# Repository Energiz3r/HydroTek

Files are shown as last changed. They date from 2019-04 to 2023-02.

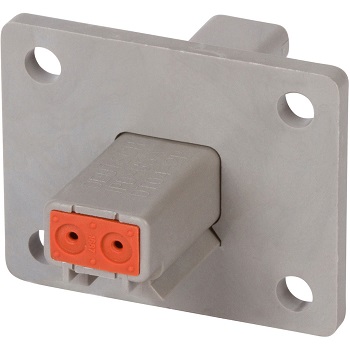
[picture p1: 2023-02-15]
pcb/DT04-2P-L012_1_1200__03789.jpg

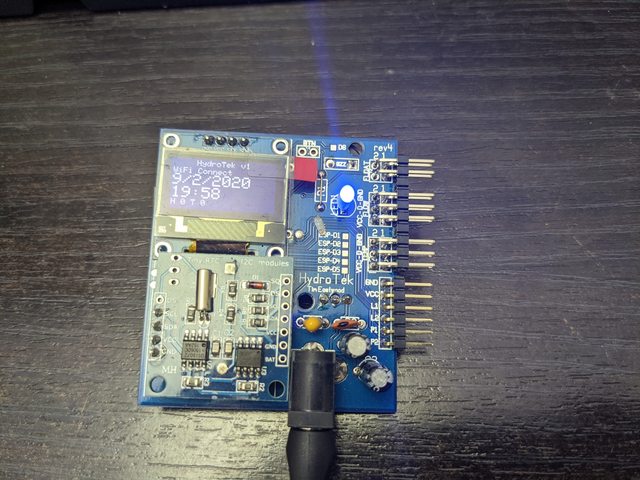
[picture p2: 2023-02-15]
pcb/rev4.jpg

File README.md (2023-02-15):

# HydroTek

## An IoT Controller for Aquaponics, Hydroponics, and Aeroponics

---

Visit [https://github.com/Energiz3r/hydrotek-react](https://github.com/Energiz3r/hydrotek-react) to access the react app which accompanies the hardware.

### Status Update:

This project is under development. If you wish to build this you should contact me to see if it's feasible at the time.
As of writing, the hardware is mostly complete, but I am designing a new PCB to address quality of life points, such as proper connectors for sensors instead of IDC header pins.
Firmware is largely finished and, with an understanding of the format of the web requests, could be made to talk to any API for updating the device configuration or just simply logging of data.
Management and reporting software comes in the form of a react / PHP / SQL based web app and is only partially complete.
Designs for the casing of the device will not be started until the PCB for the current revision is finalised and tested.

---

### Design:

There are four components to this repository:

- PCB cad file (created in PCBWeb for early revisions, then KiCad as of rev7)
- Firmware for the ESP32
- STL files for a case
- The webb app for configuration and monitoring of the device

### History:

Early revisions used an ESP8266 and an Arduino Nano, which communicated with each other over serial. Since discovering the ESP32 I've changed the design to simplify it greatly, however I suffered a consistent issue with the gerber files produced by PCBWeb which is now abandonware. New revisions are made in KiCAD.

---

### Overview:

This device is designed to control lighting and nutrient delivery in a hydroponics environment. It has been designed for use primarily with my own run-to-waste hydroponic system, however could be applied to just about any setup where the same sensors and control outputs are relevant, such as airponics, aquaponics, or even a simple vegge patch.

It's flexible enough that I've also used this to control the temperature within an enclosed container for making bread dough!

---

_latest hardware revision: 7_

(rev6 pictured below)
Powered here by USB - barrel jack connector not installed.



(rev5 pictured below)



(rev4 pictured below)



(rev3 pictured below)



---

## Device Options Menu (rev5):

https://www.youtube.com/watch?v=8toKR6Uxk_A

### Features:

- Uploads sensor data to cloud via WiFi
- 128x64 OLED display
- RTC with battery backup for control of grow light times even while offline or after power outage
- Online RTC time updates for accurate timekeeping
- Can monitor:
  - DHT22 temperature / humidity sensor
  - Liquid flow sensor (YF-S201 or any 5V based hall-effect sensor)
  - Float switch to detect either empty nutrient tank or full run-off tank
- Can control:
  - Grow light
  - Nutrient pump
- Buzzer / LED to alert user to lost WiFi signal, temperature extremes, nutrient pump faults, or full / empty nutrient / run-off tanks
- The board can be powered either through the barrel jack as designed or using a USB power source plugged into the ESP32 (Note: some USB power sources may not be sufficient to run both the HydroTek as well as relays connected)

I2C pH sensors _could_ be connected using a kit [such as this](https://www.sparkfun.com/products/10972), however pH meters are supposed to be stored in a pH-neutral storage solution. Since this means they aren't suitable for a constant-monitoring setup, pH monitoring was excluded from the feature set.

---

### Design considerations:

- The device must be maintenance-free
- Once assembled, flashed, and configured, the device must be easy to set up and use by non-technical people
- Compact size desirable. Other off-the-shelf units or open-source setups seem to be quite large

---

### To Do (not started):

- finish API development to complete the feature of updating the device configuration as changes are made to it through the web interface
- update the RTC time from online
- WiFi configuration on the device, using buttons and a menu instead of by editing the sketch
- Flow sensor calibration on the device, eg. 'pour 1L of water through the sensor then press OK'

---

### PCB Build instructions:

Note: The capacitors, barrel jack, and LM7805 can be omitted if the intention is to only run HydroTek from a reliable USB power source.

_(rev5)_

- To manufacture the PCB, upload the gerber files for the current PCB revision to a service such as [DirtyPCBs](http://dirtypcbs.com/store/pcbs)
- Purchase the components, as desired, outlined in the BOM file
- Solder the components to the PCB, ensuring the following order is observed (_B/S = BOTTOM SIDE_):
  - (B/S) Solder the LM7805 linear regulator to the UNDERSIDE of the board, ensuring the tab is soldered to the large square pad for heat dissipation
  - Solder in the 4x capacitors
  - Solder in the piezo buzzer
  - Solder in the IDC headers for the sensor inputs (to the TOP side of the board)
  - Solder in the IDC sockets for the LCD (or alternatively, solder the LCD direct to the board, if clearance above capacitors allows)
  - Solder in the ESP32
  - Solder remaining components
  - Install IDC jumper shunts between the GND and DATA pins for flow sensors that will not be used, else the pin will float and detect erroneous readings
  - If the float sensor logic is to be inverted (normally-closed), a jumper shunt on those pins will be handy to silence the alarm if the power is on and the float sensors are not connected
- Configure your Arduino IDE according to the section below
- Edit the WiFi configuration and web username / password combination in 'esp32.ino' to suit your needs, then upload to the ESP32
- Power on your HydroTek and access the web app to confirm it works
- Connect your (safe, low-voltage) lamps / pumps to the relay module and connect the relay module inputs to the header pins on the PCB
  - NOTE: If in any doubt at all, use safe, low-voltage LED grow lights and nutrient pumps. Switching of mains voltages may not be at all legal where you live, your relays may not be sufficient, I advise you not to try it, and I accept no responsibility if you do.

---

### Arduino IDE Configuration:

_(rev5)_

- Go to 'File' > 'Preferences', then click the icon to the right of the text input for "Additional board manager URLs"
- Paste the following text into the field (separate existing entries by a comma and a new line):
  > https://dl.espressif.com/dl/package_esp32_index.json
- Go to 'Tools' > 'Board...' > 'Boards Manager'
- Search for ESP32, and install the 'esp32 by Espressif Systems' package (version 1.0.2 at the time of writing)
- Go to 'Tools' > 'Board...' and select 'ESP32 Dev Module'
- Go to 'Sketch' > 'Include Library' > 'Manage Libraries'
- Search for 'Adafruit GFX' and install the 'Adafruit GFX Library' package by Adafruit
- Search for 'Adafruit 1306' and install the 'Adafruit SSD1306' package by Adafruit
- Search for 'dht22' and install the 'DHT sensor library' package by Adafruit
- Search for 'rtclib' and install the 'RTClib' package by Adafruit

- Go to 'Tools' > 'Port' and select the port for your connected ESP32
- Once you have edited the .ino file to suit your desired configuration, click upload to flash the ESP.

---

### Known issues:

_(rev5)_

- Have not designed a 3D printable case. Will not do this until satisfied the board design is final
- The react app is included in the repo for now but is incomplete and may be removed in future. Makers will be able to use my hosted platform or build their own API
- The nutrient flow values are raw 'ticks' from the flow sensor, not a calculated litres or gallons value

---

### API:

_(rev5)_

The sketch sends a POST request to the URL supplied in the variable 'webEndpoint'. The POST values are as follows:

| POST variable name | description | data type the ESP will supply |
| --- | --- | --- |
| user | username for API | string |
| password | password for API | string |
| deviceID | the ID of the device\* | int |
| t1 | temperature 1 | int or float |
| t2 | temperature 2 | int or float |
| h1 | humidity 1 | int or float |
| h2 | humidity 2 | int or float |
| f1 | float 1 | int |
| f2 | float 2 | int |
| l1 | flow 1 | int or float |
| l2 | flow 2 | int or float |

_The deviceID was only intended to be used if you wanted to have multiple devices use your endpoint._

In future, makers will be able to use my hosted platform once it is complete instead of building their own.

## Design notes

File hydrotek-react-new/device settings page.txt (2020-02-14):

data upload frequency (seconds)
email address for alerts
single plant mode enable / disable
plant 1 name
plant 2 name

temp / humidity sensor 1 enable / disable
	lamp over-temp shutoff enable / disable
		max temperature
	hi temp send email enable / disable (one must be selected)
	hi temp sound alarm enable / disable
		high temp alert temperature
	lo temp send email enable / disable (one must be selected)
	lo temp sound alarm enable / disable
		lo temp alert temperature
temp / humidity sensor 2 enable / disable
	lamp over-temp shutoff enable / disable
		max temperature
	hi temp send email enable / disable (one must be selected)
	hi temp sound alarm enable / disable
		high temp alert temperature
	lo temp send email enable / disable (one must be selected)
	lo temp sound alarm enable / disable
		lo temp alert temperature
lamp 1 enable / disable
	heater mode enable / disable
		target temperature
	start time (veg)
	end time (veg)
	veg / flower mode
		start time (flower)
		end time (flower)
	invert relay logic enable / disable
lamp 2 enable / disable
	heater mode enable / disable
		target temperature
	start time (veg)
	end time (veg)
	veg / flower mode
		start time (flower)
		end time (flower)
	invert relay logic enable / disable
nutrient pump 1 enable / disable
	mode flow / duration
		flow milli-litres
		send email if flow not achieved in time enable / disable
		sound alarm if flow not achieved in time enable / disable
	duration / max duration
	frequency (minutes)
	invert relay logic enable / disable
nutrient pump 2 enable / disable
	mode flow / duration
		flow milli-litres
		send email if flow not achieved in time enable / disable
		sound alarm if flow not achieved in time enable / disable
	duration / max duration
	frequency (minutes)
	invert relay logic enable / disable
float sensor 1 enable / disable
	audible alarm enable / disable
	pump 1 shutoff enable / disable
	invert sensor logic enable / disable
float sensor 2 enable / disable
	audible alarm enable / disable
	pump 2 shutoff enable / disable
	invert sensor logic enable / disable
flow sensor 1 enable / disable
flow sensor 2 enable / disable

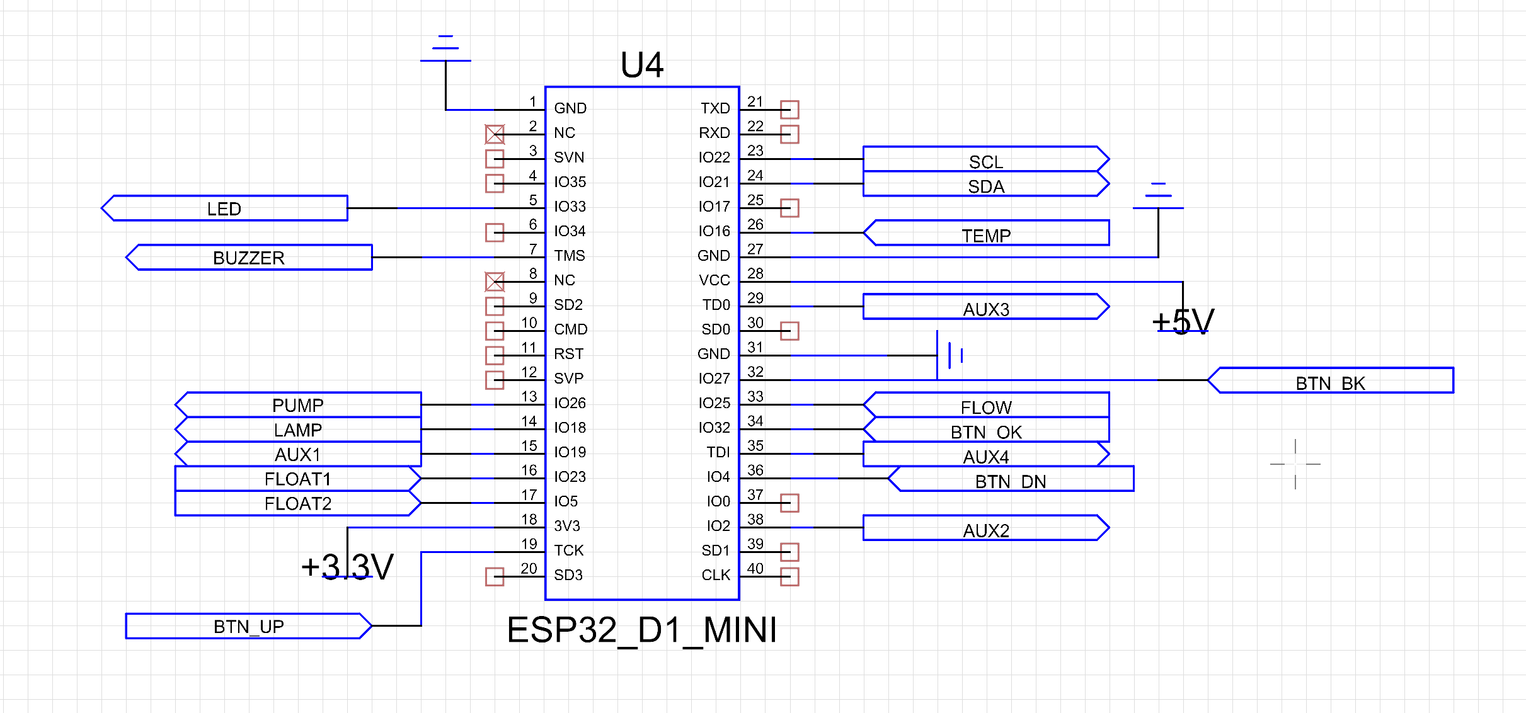
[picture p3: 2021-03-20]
pcb/kicad rev7/pinout.png

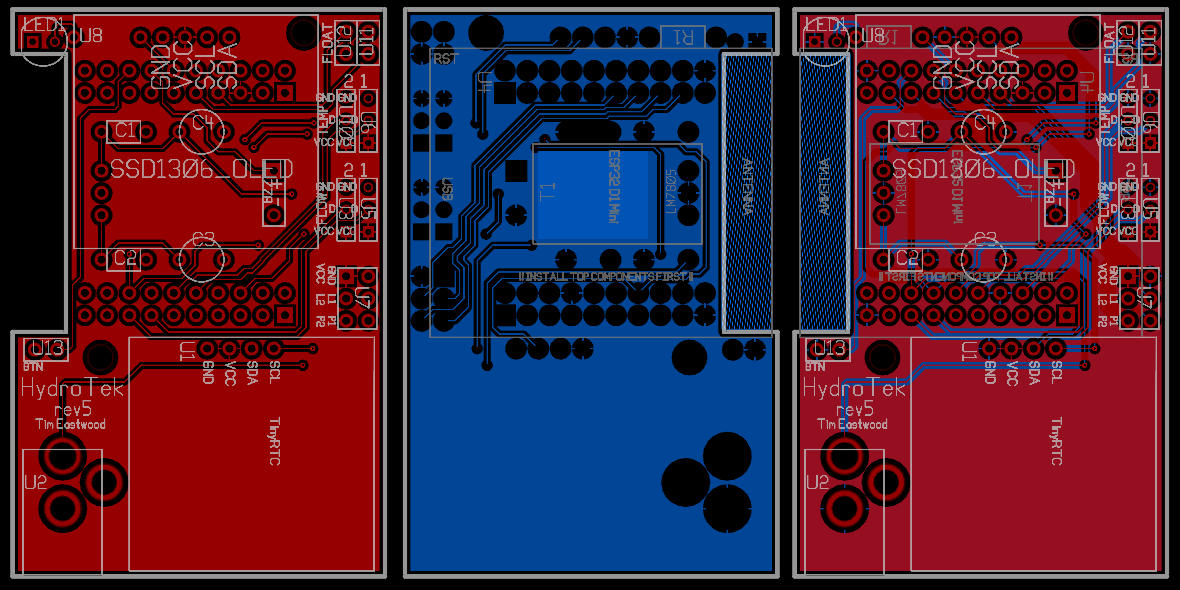
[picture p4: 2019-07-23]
pcb/pcb-rev5.png

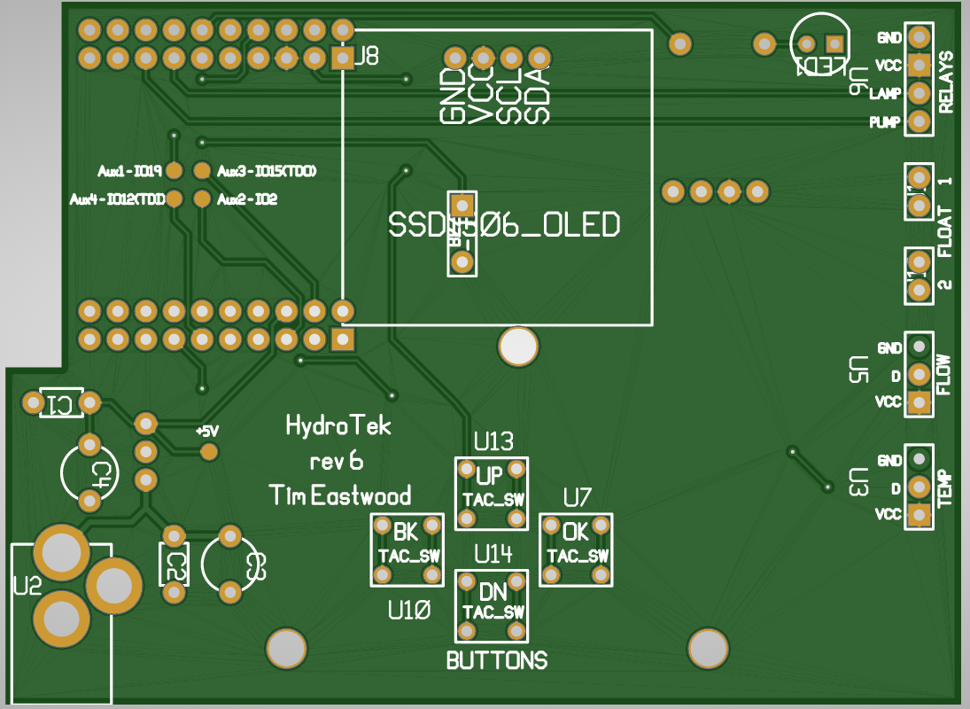
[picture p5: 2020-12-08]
pcb/pcb-rev6.png

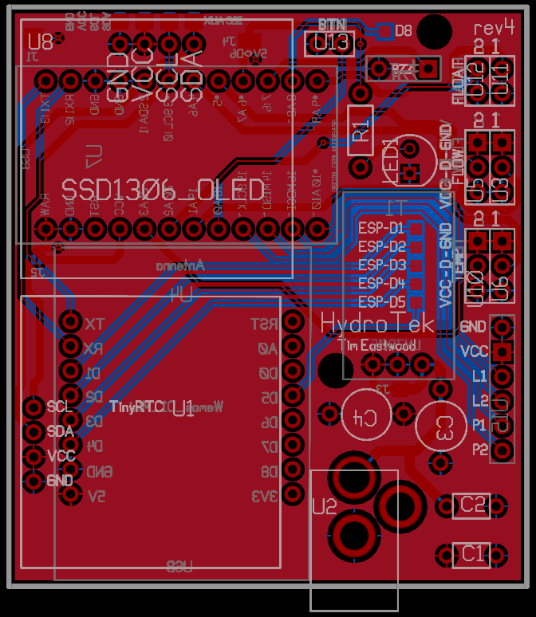
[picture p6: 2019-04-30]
pcb/pcb-rev4.png

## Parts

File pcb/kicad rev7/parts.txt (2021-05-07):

3-pin right angle molex PCB - p/n 172648-0103

MIKROE-2168 display 4.3" capacitive touch I2C
https://au.rs-online.com/web/p/lcd-colour-displays/1393635/

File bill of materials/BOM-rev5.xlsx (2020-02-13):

Bill Of Materials | rev5
Item | Source | Qty
PCB rev5 |  | 1
ESP32 - D1 mini form factor |  | 1
SSD1306 128x64 OLED, i2c |  | 1
TinyRTC + battery to suit (LRXXX) |  | 1
LM7805 through-hole |  | 1
LED (3.3v or 5v) |  | 1
Resistor for LED (if reqd) |  | 1
piezo buzzer |  | 1
50uF-100uF 16V+ low-ESR electrolytic capacitor |  | 2
.1uF ceramic disc or tantalum capacitor |  | 1
.22uF - .33uF ceramic disc or tantalum capacitor |  | 1
5.5mm barrel jack power connector |  | 1
IDC header pins 0.1" pitch (qty as needed)
IDC jumper shunts as reqd
IDC socket 0.1" pitch (4x pin long - for OLED to plug into) |  | 1
3D printed case - rev5 |  | 1
Peripherals: (qty as desired)
DHT22 |  | 2
YF-S201 flow sensor |  | 2
float sensor (on / off reed switch type, NO or NC to suit) |  | 2
4-channel relay module, 5v logic |  | 1

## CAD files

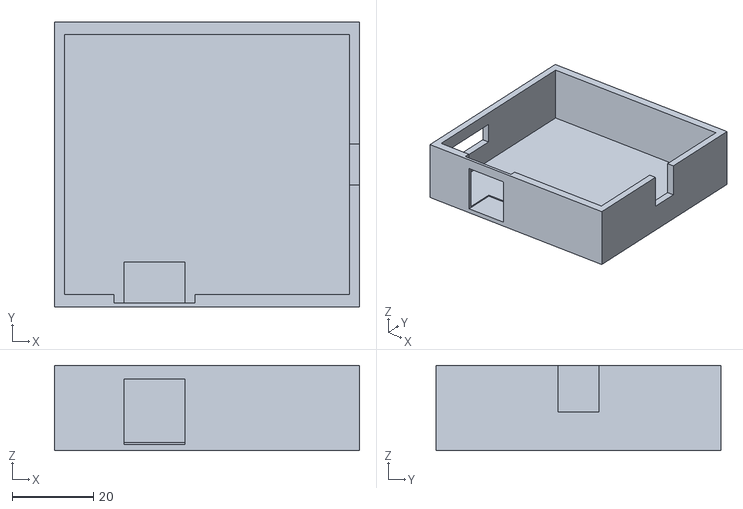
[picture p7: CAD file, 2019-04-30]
case/rev3/plant1_base3.stl
75.0 x 70.0 x 21.0

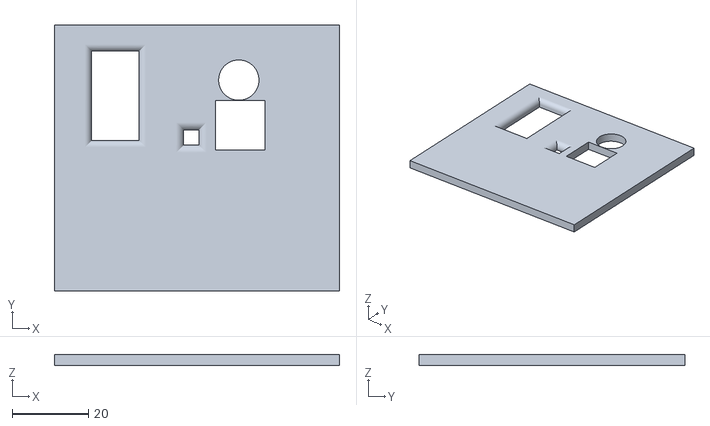
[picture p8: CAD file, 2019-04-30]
case/rev3/plant1_cover3.stl
75.0 x 70.0 x 3.00

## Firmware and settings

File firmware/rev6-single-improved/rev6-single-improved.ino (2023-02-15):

/*
 * 
 * HydroTek hydroponics controller - tim eastwood
 * 
 * See https://github.com/Energiz3r/HydroTek for information and instructions
 *
 * A lot of this code could be external or at least classes but really only the button showed a need to be classed at this time
 * Device may be released as 'single plant' further negating the need to worry about it
 * 
 * Target: ESP32 Dev Module
 * 
 * Pin assignment notes: 
 * 
 *   This sketch to suit ESP32 "D1" WeMos D1 Mini compatible
 * 
 *  4,13,18,19,23,25,26,27,32,33 - OK **19 grounded accidentally
 *  2 - OK, connected to onboard LED
 *  5,14,15 - OK, PWM at boot
 *  34,35,36,39 - input only, no pull-up/down
 *  12 - output OK, boot fail if pulled HIGH
 *  21, 22 - SDA, SCL
 *  16,17 - OK, but RX, TX UART 2
 *  
 *  
 *  
 */

#define LOOP_SPEED 50 // frequency with which to update sensors and so on (every x ms). default 50. do not change

//#define PREFERENCES_CLEAR //deprecated. can be reset from the settings menu. uncomment to erase settings from flash
//#define SET_RTC_MANUAL // uncomment to force setting the RTC time to the sketch compile time
//#define offlineMode // deprecated. wifi can be disabled from the settings menu
//#define buttonDisable

#include <pitches.h>
#include <Tone32.h>

#include "menu-option.h"

// PIN ASSIGNMENTS
#define floatSw1Pin 23 // OK
#define floatSw2Pin 5 // OK
#define dhtPin 16 // OK (dht2: 17)
#define flowPin 25 // OK (flow2: 32)
#define lampPin 18 // untested (lamp2: 18) 19 originally - bridged to ground on current PCB
#define pumpPin 26 // untested (pump2: 36)

#define ledPin 33 // not working (pin is not an output)
#define ledBrightness 20 // 0 - 255
#define buzzPin 14 // OK (TMS)
#define buttonPinOK 32 // OK
#define buttonPinBK 27 // OK
#define buttonPinUP 13 // OK (TCK)
#define buttonPinDN 4 // OK (IO4)
#define buttonDurationLong 

#define aux1 19
#define aux2 2
#define aux3 15 //(TDO)
#define aux4 12 //(TDI)
// END PIN ASSIGNMENTS

String devicePassword = "";
String deviceID = "1";
char* wifiSSID = "";
char* wifiPassphrase =  "";

#define webEndpoint "https://noobs.wtf/plants/device/upload.php" //the php script that the ESP8266 will connect to for uploading data
#define lampHeaterTempVariance 0.5 // how much to allow the temp to vary from the desired setting before switching the state of the heater (lamp)
#define buttonShortTime 30 //ms
#define buttonLongTime 250 //ms
//#define flowPulsesPerMl 0.45 //flow sensor pulses per mL of liquid (YF-S201 sensor = 0.45) //deprecated. now an item in the settings menu
#define buzzerChannel 1 // specify the PWM channel to use for the buzzer
#define screenSleepTime 1 // how long to keep screen on for before sleeping (mins)
#define buttonDebounceTime 10 //ms

// ESP WiFi Includes
#include <WiFi.h>
#include <HTTPClient.h>

// OLED display includes
#include <SPI.h>
#include <Wire.h>
#include <Adafruit_GFX.h>
#include <Adafruit_SSD1306.h>
#define SCREEN_WIDTH 128 // OLED display width, in pixels
#define SCREEN_HEIGHT 64 // OLED display height, in pixels
Adafruit_SSD1306 display(SCREEN_WIDTH, SCREEN_HEIGHT, &Wire, -1); // -1 is the reset pin, or 4 // Declaration for an SSD1306 display connected to I2C (SDA, SCL pins)

// DHT sensor includes
#include "DHT.h"
DHT dht(dhtPin, DHT22); //pin, type

// RTC includes
#include <RTClib.h>
RTC_DS1307 RTC;

// JSON includes
#include <ArduinoJson.h>

// declare an array of menu option objects
#define NUM_MENU_OPTIONS 34
MenuOption menuOptions[NUM_MENU_OPTIONS] = {
  //(int pos (menu position), String title (description), String systemName (used for the 'preferences' library), String type (bool, int, or float), float defaultVal, float maxVal, float minVal, bool showInMenu, bool saveInFlash
  
  (1, "Upload frequency", "uploadFreq", "int", 30, 1, true, true),
  //temp
  (2, "Temp enable", "tenable", "bool", 0, 0.0, true, true),
  (3, "HI Temp lamp off", "tlampshutoff", "bool", 0, 0, true, true),
  (4, "Shutoff Temp degC", "tshutofftemp", "float", 60, 5, true, true),
  (5, "HI temp alarm", "thighalarm", "bool", 0, 0, true, true),
  (6, "HI Temp degC", "thightemp", "float", 60, 5, true, true),
  (7, "LO temp alarm", "tlowalarm", "bool", 0, 0, true, true),
  (8, "HI Temp degC", "tlowtemp", "float", 60, 5, true, true),
  //lamp
  (9, "Lamp enable", "lenable", "bool", 0, 0, true, true),
  (10, "Lamp is heater", "lheater", "bool", 0, 0, true, true),
  (11, "Heater temp degC", "ltemp", "float", 60, 5, true, true),
  (12, "Lamp on hour", "lstarthour", "int", 23, 0, true, true),
  (13, "Lamp off hour", "lendhour", "int", 23, 0, true, true),
  (14, "Lamp invert", "linvert", "bool", 0, 0, true, true),
  //pump
  (15, "Pump enable", "penable", "bool", 0, 0, true, true),
  (16, "Pump flow mode", "pflow", "bool", 0, 0, true, true),
  (17, "Pump flow Ml", "pflowml", "int", 5000, 0, true, true),
  (18, "Pump alarm", "pflowalarm", "bool", 0, 0, true, true),
  (19, "Pump duration sec", "pduration", "int", 240, 5, true, true),
  (20, "Pump freq. min", "pfrequency", "int", 240, 2, true, true),
  (21, "Pump invert", "pinvert", "bool", 0, 0, true, true),
  //float 1
  (22, "Float1 enable", "flt1enable", "bool", 0, 0, true, true),
  (23, "Float1 alarm", "flt1alarm", "bool", 0, 0, true, true),
  (24, "Float1 pump off", "flt1shutoff", "bool", 0, 0, true, true),
  (25, "Float1 invert", "flt1invert", "bool", 0, 0, true, true),
  //float 2
  (26, "Float2 enable", "flt2enable", "bool", 0, 0, true, true),
  (27, "Float2 alarm", "flt2alarm", "bool", 0, 0, true, true),
  (28, "Float2 pump off", "flt2shutoff", "bool", 0, 0, true, true),
  (29, "Float2 invert", "flt2invert", "bool", 0, 0, true, true),
  //flow
  (30, "Flow enable", "flwenable", "bool", 0, 0, true, true),
  (31, "Flow pulses per Ml", "flowpulsesml", "float", 1000, 0, true, true),
  //system
  (32, "Select display type", "displaytype", "int", 1, 0, true, true),
  (33, "Enable WiFi", "enablewifi", "bool", 0, 0, true, true),
  (34, "Reset Settings", "reset", "bool", 0, 0, true, false)
}

// return title
String getMenuOptionTitle(int menuPos) {
  for (int i = 0; i < NUM_MENU_OPTIONS; i ++) {
    if (menuOptions[i].pos() == menuPos) {
      return menuOptions[i].title();
    }
  }
  return "Menu Error";
}

// increment or decrement a menu option
void incrementMenuOption(int menuPos, bool increment) {
  for (int i = 0; i < NUM_MENU_OPTIONS; i ++) {
    if (menuOptions[i].pos() == menuPos) {
      if (menuPos == 34) { // reset all settings
        Serial.println("Erasing flash and rebooting..."); preferences.clear(); ESP.restart(); // delete everything in the flash and reboot the ESP to recreate the structure
      } else {
        menuOptions[i].adjustVal(increment);
      }
    }
  }
}

// returns value as a String (for use on the display)
const String stringEnabled = "Enabled";
const String stringDisabled = "Disabled"; // used this instead of a #define because I'm pretty sure this takes up less space in the sketch
String getMenuOptionValue(int menuPos) {
  for (int i = 0; i < NUM_MENU_OPTIONS; i ++) {
    if (menuOptions[i].pos() == menuPos) {
      if (menuPos == 34) { // reset all settings
        return "";
      } else {
        String type = menuOptions[i].getType();
        if (type == "bool") {
          return menuOptions[i].boolVal() ? stringEnabled : stringDisabled;
        } else if (type == "int") {
          return String(menuOptions[i].intVal());
        } else if (type == "float" ) {
          return String(menuOptions[i].floatVal());
        }
      }
    }
  }
  return "Menu Error";
}

// read settings from flash memory using 'preferences' library
void flashRead() {
  Serial.println("Reading flash...");
  for (int i = 0; i < NUM_MENU_OPTIONS; i ++) {
    if (menuOptions[i].saveInFlash()) {
      String type = menuOptions[i].getType();
      String systemName = menuOptions[i].getSysName();
      if (type == "bool") {
        menuOptions[i].setBoolVal(preferences.getBool(systemName, menuOptions[i].defaultVal() == 1 ? true : false;));
      } else if (type == "int") {
        menuOptions[i].setIntVal(preferences.getUInt(systemName, Int(menuOptions[i].defaultVal())));
      } else if (type == "float" ) {
        menuOptions[i].setIntVal(preferences.getFloat(systemName, menuOptions[i].defaultVal()));
      }
    }
  }
  Serial.println("Loaded settings from flash!");
}

// write settings to flash memory
void flashWrite() {
  Serial.println("Writing flash...");
  for (int i = 0; i < NUM_MENU_OPTIONS; i ++) {
    if (menuOptions[i].saveInFlash()) {
      String type = menuOptions[i].getType();
      String systemName = menuOptions[i].getSysName();
      if (type == "bool") {
        preferences.putBool(systemName, menuOptions[i].boolVal())
      } else if (type == "int") {
        preferences.putUInt(systemName, menuOptions[i].intVal())
      } else if (type == "float" ) {
        preferences.putFloat(systemName, menuOptions[i].floatVal())
      }
    }
  }
  Serial.println("Wrote settings to flash!");
}

void onButtonPress(String btnType, bool longPress);
class Button {
  public:
    int Init(int pin, String type);
    void checkState(unsigned int long curMs);
  private:
    int _pin;
    String _btnType;
    unsigned int long _startTime;
    bool _lastState;
};

int Button::Init(int pin, String type) {
  _pin = pin;
  _btnType = type;
  _startTime = 0;
  _lastState = false;
  pinMode(pin, INPUT_PULLUP);
}

void Button::checkState(unsigned int long curMs) {
  if (digitalRead(_pin) == LOW && !_lastState) {
    _startTime = curMs;
    _lastState = true;
  }
  //button released
  if (digitalRead(_pin) == HIGH && _lastState) {
    if (curMs - _startTime > buttonShortTime) {
//      if (curMs - _startTime > buttonLongTime) {
//        tone(buzzPin, 800, 250);
//        onButtonPress(_btnType, true);
//      } else {
        tone(buzzPin, NOTE_C5, 10, buzzerChannel);
        noTone(buzzPin, buzzerChannel);
        onButtonPress(_btnType, false);
      //}
    }
    _lastState = false;
  }
}

Button buttonOK;
Button buttonBK;
Button buttonUP;
Button buttonDN;

void webConfigRead() {
//  webUsername = preferences.getString("webUser", "");
//  webPassword = preferences.getString("webPass", "");
//  webDeviceID = preferences.getString("webDevice", "");
//  wifiSSID = preferences.getChar("wifiSSID", "");
//  wifiPassphrase =  preferences.getChar("wifiPass", "");
}
void webConfigWrite() {
//  preferences.putString("webUser", webUsername);
//  preferences.putString("webPass", webPassword);
//  preferences.putString("webDevice", webDeviceID);
//  preferences.putChar("wifiSSID", wifiSSID);
//  preferences.putChar("wifiPass", wifiPassphrase);
}

//update config from online
String webError = "";
bool configDownloaded = false;
void handleReceiveConfig(String webResponse) {

  const size_t capacity = JSON_OBJECT_SIZE(51) + 1210;
  DynamicJsonDocument doc(capacity);

  deserializeJson(doc, webResponse);

  //check if parsing the JSON failed
  JsonObject object = doc.as<JsonObject>();
  if (object.isNull()) {
    webError = "Error: ";
    webError += webResponse;
    Serial.println(webError);
    configDownloaded = false;
    return;
  }

  configUploadFrequencyMins.setIntVal( doc["configUploadFrequencyMins"]);
  // etc...

  Serial.println("Updated config:");
  Serial.println(webResponse);

  configDownloaded = true;
  webError = "";

  flashWrite();
}

#define firstCoordinate 0
#define charHeight 8
#define titleBarHeight 11
#define lineX 2
int lineY(int line) { 
  if (line == 1) { return firstCoordinate + titleBarHeight + 1; }
  if (line == 2) { return lineY(1) + charHeight; }
  if (line > 2) { return lineY(line - 1) + charHeight; }
}

//draws the border and title etc
bool wifiConnected = false;
bool inMenu = false;
String menuTitle = "";
void drawInitial() {
  display.clearDisplay();
  display.drawRoundRect(0,0,display.width(),display.height(), 2, WHITE); //x, y, x, y, radius, color
  display.fillRoundRect(0,0,display.width(),10, 2, WHITE); //x, y, x, y, radius, color
  display.setTextColor(BLACK); // Draw black text (background transparent by default)
  display.setCursor(27, 2); //title line
  String title = inMenu ? menuTitle : "HydroTek rev5";
  display.print(title);
  display.setCursor(3, 2); //title line
  if (wifiConnected) { display.print("+"); } else { display.print("-"); }
  if (configDownloaded) { display.print("+"); } else { display.print("-"); }
  display.setTextColor(WHITE, BLACK); // Draw white text with a black background 
}

float temp;
float humidity;
void tempCheckState() {
  if (configTempEnable.boolVal()) {
    temp = dht.readTemperature(); //read temperature as Celsius (the default)
    humidity = dht.readHumidity(); //read humidity
    if (isnan(temp)) { temp = 0.0; }
    if (isnan(humidity)) { humidity = 0.0; }
  }
}

//turn lamp relay(s) on / off
bool lampLastState = false;
void lampSetState (String stateStr) {
  bool state = stateStr == "ON";
  bool invertLogic = configLampInvertLogic.boolVal();
  //Serial.println("Lamp invert: " + String(invertLogic));
  bool tempOverride = false;
  if (!configLampHeaterMode.boolVal() && configTempEnable.boolVal() && configTempLampShutoff.boolVal() && temp > configTempLampShutoffTemp.floatVal()) {
    tempOverride = true;
  }
  if (!invertLogic) {
    if (state && !tempOverride) {
      digitalWrite(lampPin, LOW);
      lampLastState = true;
    } else {
      digitalWrite(lampPin, HIGH);
      lampLastState = false;
    }
  } else {
    if (state && !tempOverride) {
      digitalWrite(lampPin, HIGH);
      lampLastState = true;
    } else {
      digitalWrite(lampPin, LOW);
      lampLastState = false;
    }
  }
}

void lampCheckState (int currentHour) {
  if (configLampEnable.boolVal()) {
    if (configLampHeaterMode.boolVal()) {
      if (configTempEnable.boolVal()) {
        if (temp > configLampHeaterTemp.floatVal() + lampHeaterTempVariance) {
          lampSetState("OFF");
        } else if (temp < configLampHeaterTemp.floatVal() - lampHeaterTempVariance) {
          lampSetState("ON");
        }
      }
    } else {
      if (configLampEndHour.intVal() > configLampStartHour.intVal()) {
        if (currentHour < configLampEndHour.intVal() && currentHour >= configLampStartHour.intVal()) {
          lampSetState("ON");
        } else {
          lampSetState("OFF");
        }
      }
      else if (configLampEndHour.intVal() < configLampStartHour.intVal()) {
        if (currentHour >= configLampStartHour.intVal() || currentHour < configLampEndHour.intVal()) {
          lampSetState("ON");
        } else {
          lampSetState("OFF");
        }
      }
    }
  } else {
    lampSetState("OFF");
  }
}

//float sensor variables
bool float1triggered = false;
bool float2triggered = false;

//sounds alarm if conditions are met
bool pumpMissedFlowTarget = false;
String alarmReason = "";
void alarmCheckState(){
  bool shouldSoundAlarm = false;
  alarmReason = "";
  if (!wifiConnected && configEnableWifi.boolVal()) {
    alarmReason = "WiFi Disconnected";
  } else if (configEnableWifi.boolVal()) {
    if (configDownloaded) {
      alarmReason = "Sync OK";
    } else {
      #ifdef offlineMode
        alarmReason = "Offline Mode";
      #else
        alarmReason = "Sync Error";
      #endif
    }
  }
  if (configTempEnable.boolVal() && configTempHighTempAlarm.boolVal() && temp > configTempHighTemp.floatVal()) {
    shouldSoundAlarm = true;
    alarmReason = "Temp HIGH";
  }
  if (configFloat1Enable.boolVal() && float1triggered) {
    if (configFloat1Alarm.boolVal()) {
      shouldSoundAlarm = true;
    }    
    alarmReason = "Tank 1 FULL/EMPTY";
  }
  if (configFloat2Enable.boolVal() && float2triggered) {
    if (configFloat2Alarm.boolVal()) {
      shouldSoundAlarm = true; 
    }
    alarmReason = "Tank 2 FULL/EMPTY";
  }
  if (pumpMissedFlowTarget) {
    shouldSoundAlarm = true;
    alarmReason = "Pump LOW FLOW";
  }
  if (shouldSoundAlarm) {
    tone(buzzPin, NOTE_A4, 50, buzzerChannel);
    noTone(buzzPin, buzzerChannel);
  }
}

bool pumpLastState = false;
void pumpSetState(String state) {
  if (!configPumpInvertLogic.boolVal() && state == "ON") {
    digitalWrite(pumpPin, LOW);
    pumpLastState = true;
  } else if (!configPumpInvertLogic.boolVal() && state == "OFF") {
    digitalWrite(pumpPin, HIGH);
    pumpLastState = false;
  } else if (configPumpInvertLogic.boolVal() && state == "ON") {
    digitalWrite(pumpPin, HIGH);
    pumpLastState = true;
  } else if (configPumpInvertLogic.boolVal() && state == "OFF") {
    digitalWrite(pumpPin, LOW);
    pumpLastState = false;
  }
}

unsigned int pumpMeasuredFlowMl = 0;
int pumpMissedTargetByMl = 0;
void pumpCheckState(DateTime now) {
  if (inMenu) { return; }
  int currentSecond = now.hour() * 60 * 60 + now.minute() * 60 + now.second();
  if (configPumpEnable.boolVal()) {
    bool pumpShouldRun = false;
    for (int i = 0; i <= 86400; i = i + configPumpFrequencyMin.intVal() * 60) {
      if (currentSecond >= i && currentSecond <= i + configPumpDurationSec.intVal()) {
        if (configPumpFlowMode.boolVal()) {
          if (pumpMeasuredFlowMl < configPumpFlowMl.intVal()) {
            pumpShouldRun = true;
          }
          //if it's within the last second of run time and the flow hasn't met the target by more than 5ml, consider the flow target not met
          if (currentSecond > i + configPumpDurationSec.intVal() - 2 && configPumpFlowMl.intVal() - pumpMeasuredFlowMl > 5) {
            pumpMissedFlowTarget = true;
            pumpMissedTargetByMl = configPumpFlowMl.intVal() - pumpMeasuredFlowMl;
          }
        } else {
          pumpShouldRun = true;
        }
      }
    }
    if (pumpShouldRun) {
      pumpSetState("ON");
    } else {
      pumpSetState("OFF");
      pumpMeasuredFlowMl = 0;
    }
  }
}

unsigned int flowPulseCount = 0;
unsigned int flowMlSinceLastUpload = 0;
void flowCheckState(){
  if (configFlowEnable.boolVal()) {
    int flowInMl = flowPulseCount / configFlowPulsesPerMl.floatVal();
    pumpMeasuredFlowMl = pumpMeasuredFlowMl + flowInMl;
    flowMlSinceLastUpload = flowMlSinceLastUpload + flowInMl;
    flowPulseCount = 0;
  }
  //(pulsesOver1000ms * 60 / 7.5); //the LPH calculation for flow sensors
}
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
void loop () {

  unsigned int long curMillis = millis();

  if (millis() - lastSerialUpdate > 60000) {
    String upd = "";
    upd = "Temp: " + String(temp) + " Target: " + String(configLampHeaterTemp.floatVal());
    Serial.println(upd);
    lastSerialUpdate = millis();
  }

  if (curMillis - screenSleepLastAction > screenSleepTime * 60 * 1000) {
    screenIsSleeping = true;
  }

  if (configEnableWifi.boolVal()) {
    if (!wifiConnOnce) {
      if (curMillis > 1000 * 60 * 2) { // if WiFi hasn't connected after 2 minutes, hard-reset the ESP
          ESP.restart();
      }
    }

    if (!calledWifiBegin && millis() > 4000) {
      WiFi.begin(wifiSSID, wifiPassphrase);
      calledWifiBegin = true;
    }
  }

  //monitor for changes to state on the flow sensor inputs
  // this *should* be an interrupt but the loop runs fast enough that it isn't really an issue, and in this case the accuracy of the flow sensor was already poor
  if (configFlowEnable.boolVal()) {
    if (digitalRead(flowPin) != flowLastState) {
      flowLastState = !flowLastState;
      if (flowLastState) { //only increment on a HIGH reading
        if (calibratingFlowSensor) {
          flowSensorCalibrationPulses++;
        }
        flowPulseCount++;
      }
    }
  }

  //OK button down
  buttonOK.checkState(curMillis);
  buttonBK.checkState(curMillis);
  buttonUP.checkState(curMillis);
  buttonDN.checkState(curMillis);

  //update sensors and display every x ms
  if (curMillis - lastSensorUpdate > LOOP_SPEED || lastSensorUpdate == 0) {
    lastSensorUpdate = curMillis;

    //check the WiFi status
    if (configEnableWifi.boolVal()) {
      if (calledWifiBegin && WiFi.status() == WL_CONNECTED) {
        wifiConnected = true;
        if (!wifiConnOnce) {
          wifiConnOnce = true;
        }
      } else {
        wifiConnected = false;
      }
    }

    DateTime now = RTC.now(); 

    //get temp and humidity readings
    tempCheckState();

    //check float sensor state
    floatCheckState();

    //update lamp states
    lampCheckState(now.hour());

    //update flow readings
    flowCheckState();

    //update pump states
    pumpCheckState(now);

    //sound any alarms
    alarmCheckState();

    //write to the display
    displayUpdate(now, curMillis);

    //upload to server
    if (configEnableWifi.boolVal()){
      uploadData(curMillis);
    }

  }

}

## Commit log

2019-04-29 Updated PCB, added STL
    [plant1_base3.stl, plant1_cover3.stl]
2019-04-30 Added rev4
    [BOM-rev3.xlsx, BOM-rev4.xlsx, plant1_base3.stl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]
2019-04-30 PCB Updated
2019-04-30 Gerber Updated
    [l1m.GTL, l2m.GBL, sm1.GTS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]
2019-05-08 updated PCB
2019-05-15 Updated PCB
    fixed pin issues, reassigned pins
2019-05-21 Added ESP32
2019-05-22 PCB update
2019-05-23 ESP32 Update
2019-07-22 PCB rev5 completed
2019-07-22 rev5 firmware for ESP32 updated
2019-07-23 Updated documentation
    [BOM-rev3.xlsx, BOM-rev4.xlsx, BOM-rev5.xlsx]
2020-03-16 react - custom toggle switch
2020-03-16 react - routemgr - eagle cad
    [rev6.kicad_pcb, rev6.sch]
2021-03-20 updated all packages, added ESP32 lib to kicad file
    [rev6.sch]
2021-03-20 Readme updated
    [rev6.kicad_pcb, rev6.sch]
2021-05-07 Started rev7 PCB. Updated dev environment and build scripts for cloud app
    [rev7.kicad_pcb, rev7.sch]
2021-05-31 Updated project structure
    [BOM-rev3.xlsx, BOM-rev4.xlsx]
